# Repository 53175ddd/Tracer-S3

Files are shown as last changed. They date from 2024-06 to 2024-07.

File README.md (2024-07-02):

# 基板概要

JLCPCB の PCBA に対応した，私 [MOS](https://x.com/53175ddd) 作成のオリジナルライントレーサです  
表面実装部品（ESP32-S3 モジュール・SMD 抵抗・コンデンサ・レギュレータ・ダイオード）のみ PCBA で実装してくれるようにしています  
それ以外の部品については下記部品表を参考に，必要に応じて部品を変更するなどしてご利用ください

# イメージ

<div align="center">
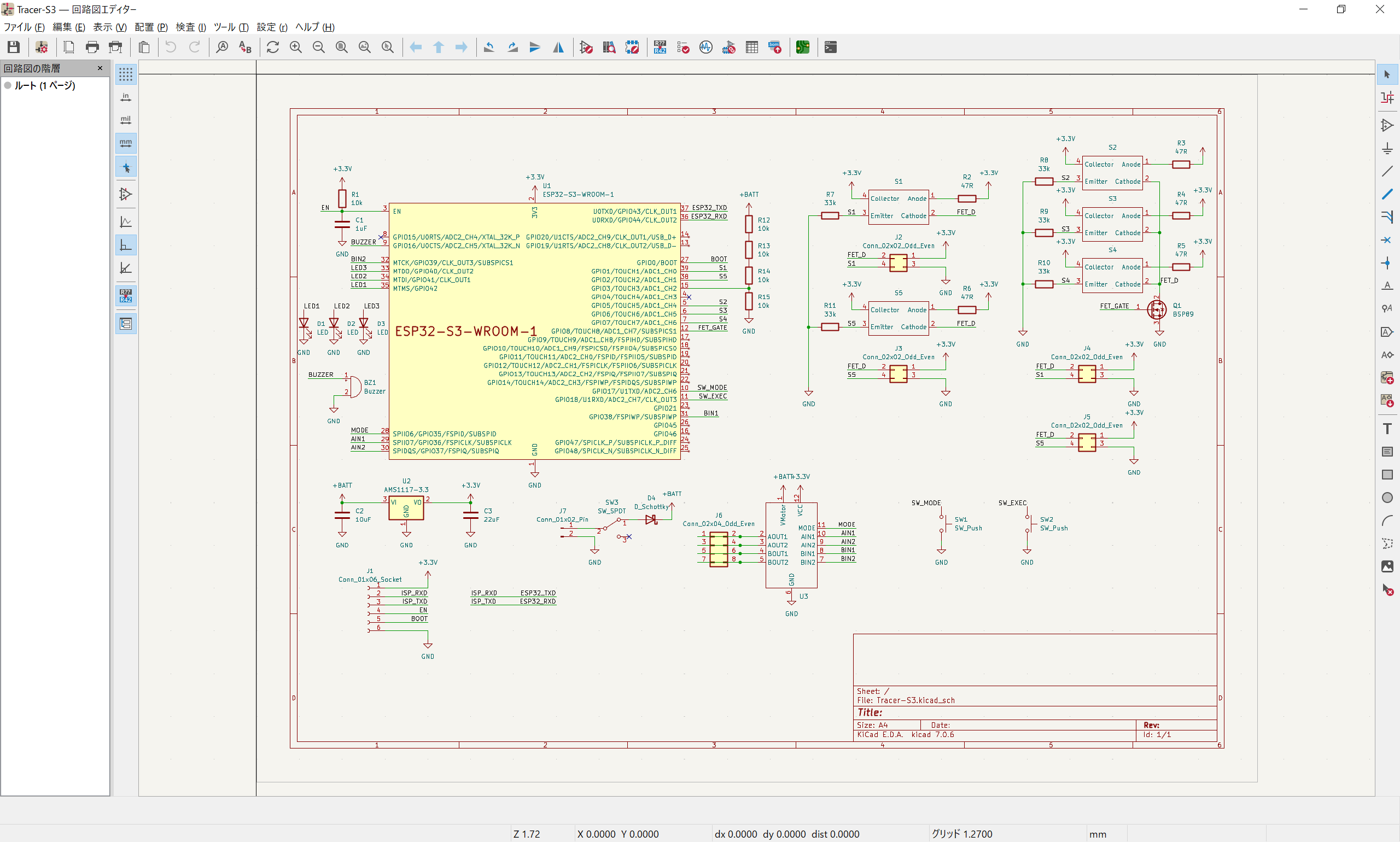
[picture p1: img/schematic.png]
  
</div>

# 部品表

| 部品番号 | 定数 | 秋月 |
|----|----|----|
| R2 ~ R6 | 47Ω 1/4W | <https://akizukidenshi.com/catalog/g/g125470/> |
| R7 ~ R11 | 3.3kΩ ~ 4.7kΩ 1/4W | 省略 |
| SW1, SW2 | タクトスイッチ | <https://akizukidenshi.com/catalog/g/g103648/> |
| SW3 | DPDT スイッチ | <https://akizukidenshi.com/catalog/g/g102627/> |
| Q1 | MOSFET | <https://akizukidenshi.com/catalog/g/g107597/> |
| U3 | モータドライバ DRV8835 | <https://akizukidenshi.com/catalog/g/g109848/> |
| BZ1 | ブザー | <https://akizukidenshi.com/catalog/g/g104118/> |
| J1 | 1x6 ピンソケット | <https://akizukidenshi.com/catalog/g/g103784/> |
| J2, J3 | 2x2 ピンヘッダ | <https://akizukidenshi.com/catalog/g/g116792/> |
| J6 | 2x4 ピンヘッダ | <https://akizukidenshi.com/catalog/g/g116793/> |
| J7 | バッテリコネクタ | 使用するバッテリに合うものを使用してください |
| D1 ~ D3 | 5V 抵抗内蔵 LED | <https://akizukidenshi.com/catalog/g/g106247/> |
| S1 ~ S5 | フォトセンサ LBR-127HLD | <https://akizukidenshi.com/catalog/g/g104500/> |

# その他部品

- タミヤ ギアボックス
- Li-Po バッテリ（2S）など
- Stamp ISP

がそれぞれ必要になります

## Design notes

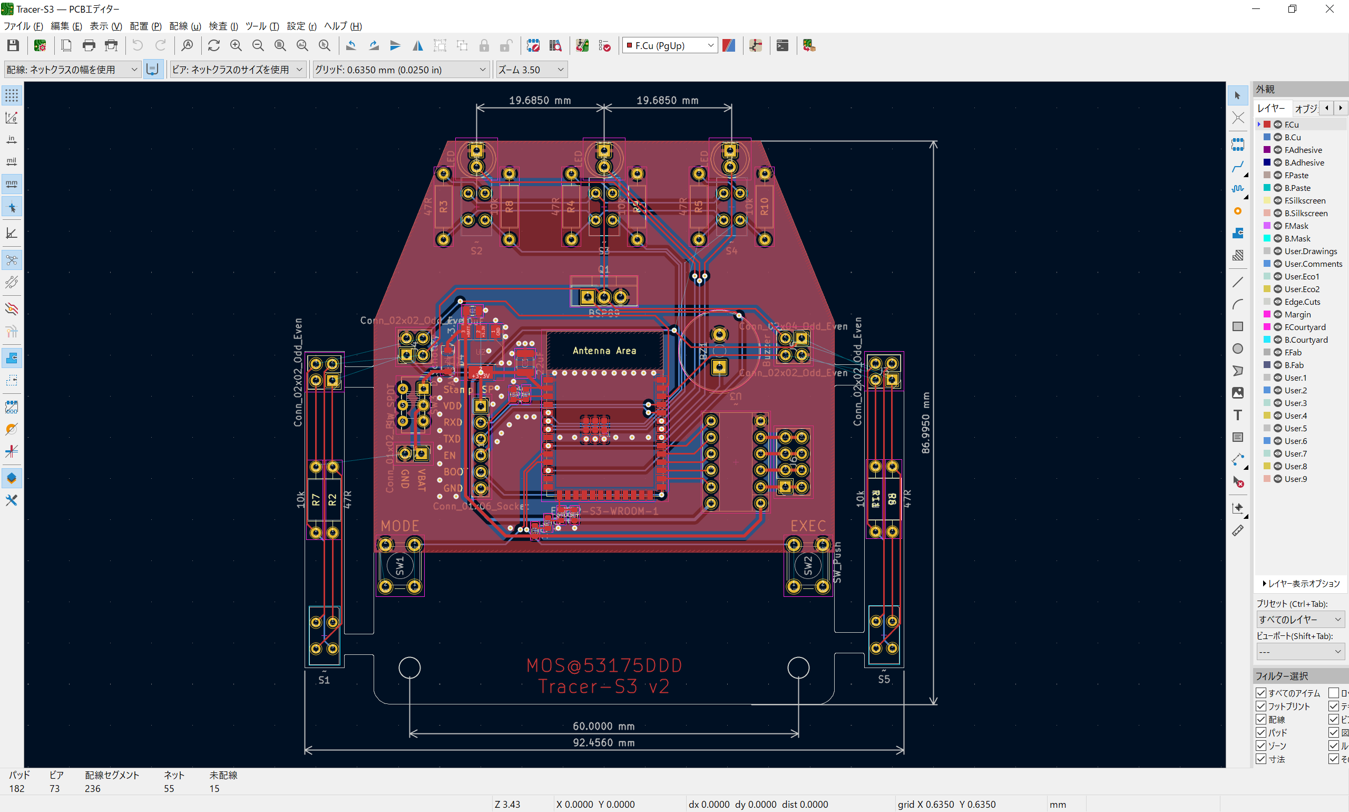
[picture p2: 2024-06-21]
img/pcb_editor.png

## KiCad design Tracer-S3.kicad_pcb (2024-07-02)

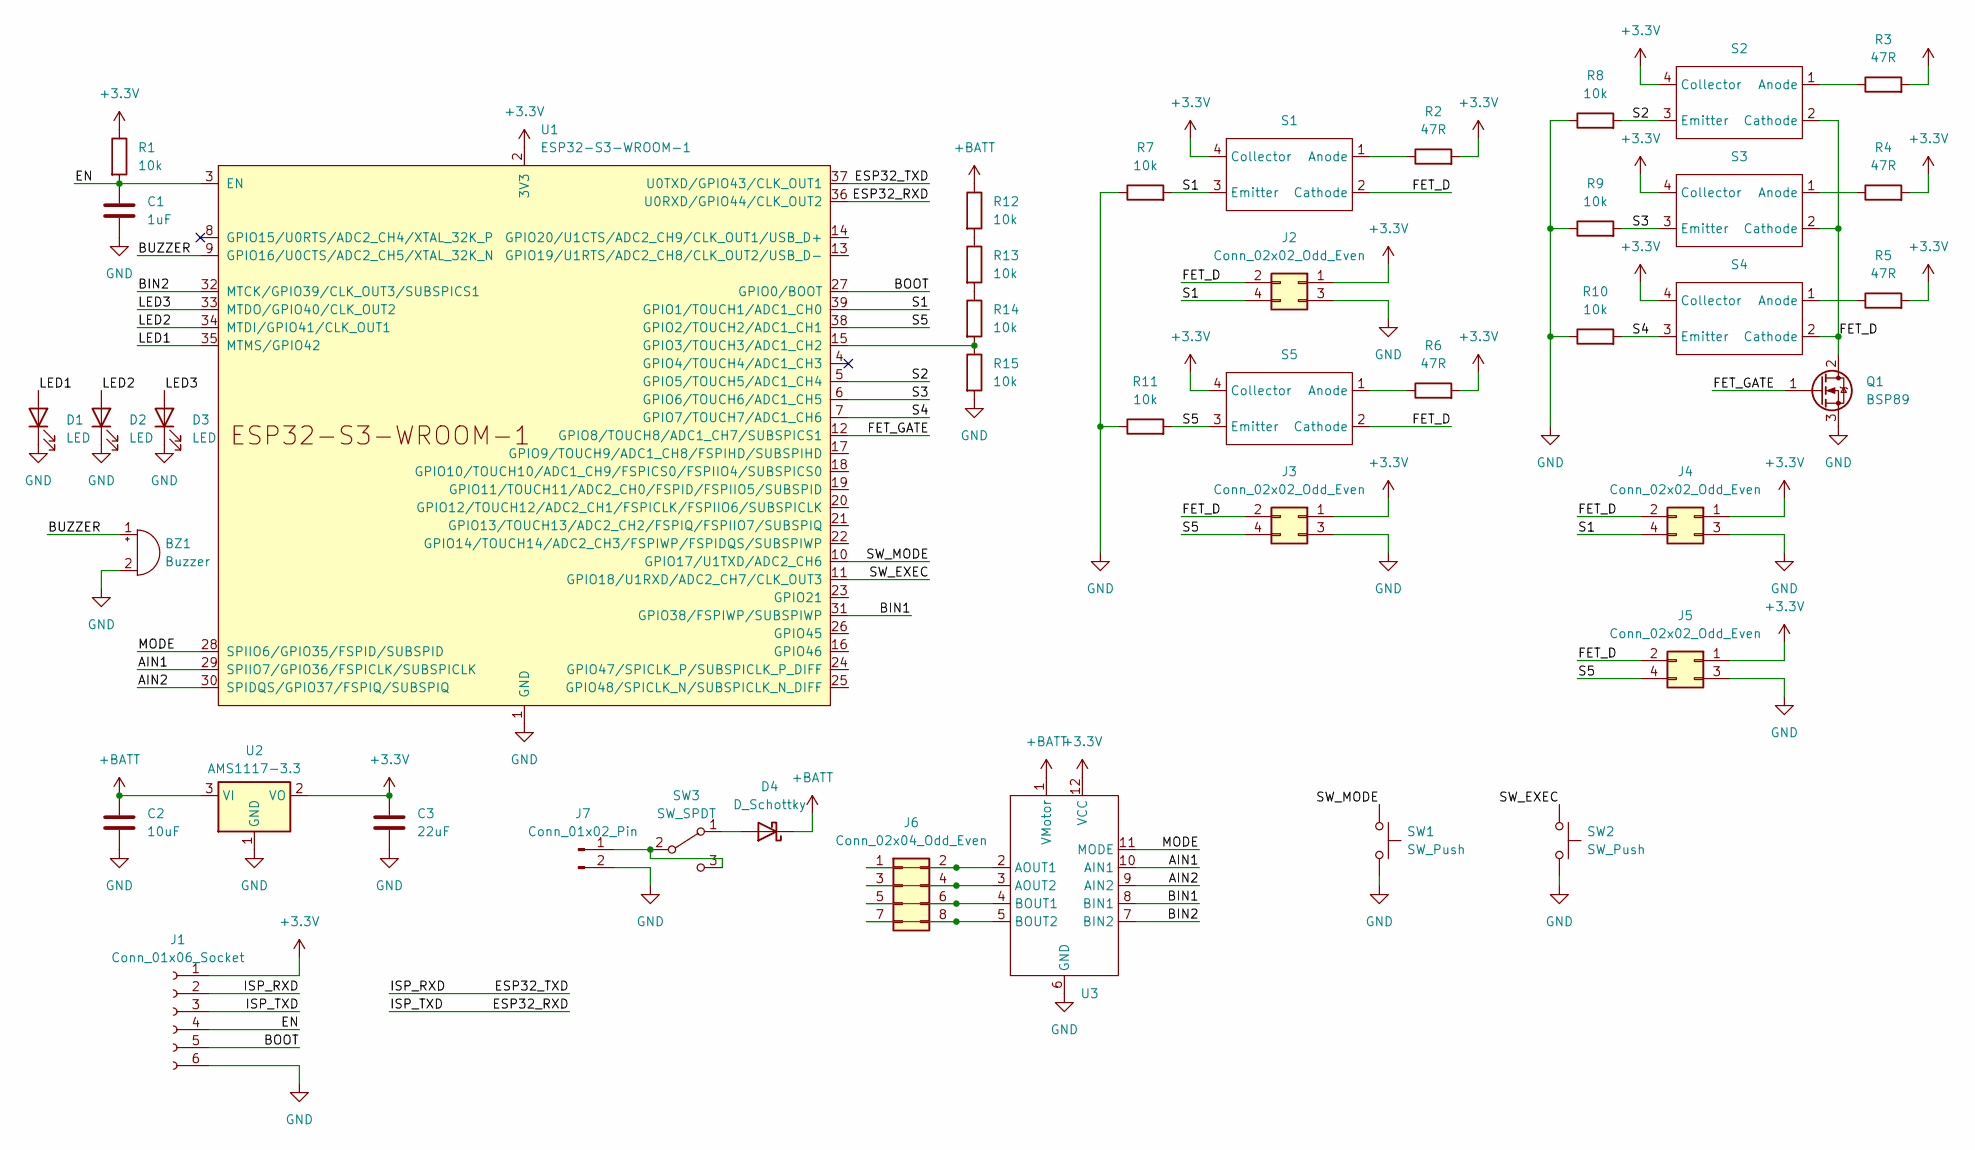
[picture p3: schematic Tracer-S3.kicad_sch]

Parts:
BZ1: Buzzer; Buzzer_TDK_PS1240P02BT_D12.2mm_H6.5mm
C1: 1uF; C_0603_1608Metric; LCSC C908011
C2: 10uF; C_0805_2012Metric; LCSC C162317
C3: 22uF; C_1210_3225Metric; LCSC C703078
D1, D2, D3: LED; LED_D5.0mm
D4: D_Schottky; D_SOD-123; LCSC C963381
J1: Conn_01x06_Socket; PinSocket_1x06_P2.54mm_Vertical
J2, J3, J4, J5: Conn_02x02_Odd_Even; PinSocket_2x02_P2.54mm_Vertical
J6: Conn_02x04_Odd_Even; PinSocket_2x04_P2.54mm_Vertical
J7: Conn_01x02_Pin; PinHeader_1x02_P2.54mm_Vertical
Q1: BSP89; TO-220-3_Vertical
R1, R12, R13, R14, R15: 10k; R_0603_1608Metric; LCSC C269701
R2, R3, R4, R5, R6: 47R; R_Axial_DIN0207_L6.3mm_D2.5mm_P10.16mm_Horizontal
R7, R8, R9, R10, R11: 10k; R_Axial_DIN0207_L6.3mm_D2.5mm_P10.16mm_Horizontal
S1, S2, S3, S4, S5: LBR-127HLD
SW1, SW2: SW_Push; SW_PUSH_6mm
SW3: SW_SPDT; SW_E-Switch_EG1271_SPDT
U1: ESP32-S3-WROOM-1
U2: AMS1117-3.3; SOT-223-3_TabPin2; LCSC C7432020
U3: AE-DRV8835

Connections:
+3.3V: C3.1, J1.1, J2.1, J3.1, J4.1, J5.1, R1.1, R2.2, R3.2, R4.2, R5.2, R6.2, S1.4 (Collector), S2.4 (Collector), S3.4 (Collector), S4.4 (Collector), S5.4 (Collector), U1.2 (3V3), U2.2 (VO), U3.12 (VCC)
+BATT: C2.1, D4.1 (K), R12.1, U2.3 (VI), U3.1 (VMotor)
/AIN1: U1.29 (SPIIO7/GPIO36/FSPICLK/SUBSPICLK), U3.10 (AIN1)
/AIN2: U1.30 (SPIDQS/GPIO37/FSPIQ/SUBSPIQ), U3.9 (AIN2)
/BIN1: U1.31 (GPIO38/FSPIWP/SUBSPIWP), U3.8 (BIN1)
/BIN2: U1.32 (MTCK/GPIO39/CLK_OUT3/SUBSPICS1), U3.7 (BIN2)
/BOOT: J1.5, U1.27 (GPIO0/BOOT)
/BUZZER: BZ1.1 (-), U1.9 (GPIO16/U0CTS/ADC2_CH5/XTAL_32K_N)
/EN: C1.1, J1.4, R1.2, U1.3 (EN)
/ESP32_RXD: J1.3, U1.36 (U0RXD/GPIO44/CLK_OUT2)
/ESP32_TXD: J1.2, U1.37 (U0TXD/GPIO43/CLK_OUT1)
/FET_D: J2.2, J3.2, J4.2, J5.2, Q1.2 (D), S1.2 (Cathode), S2.2 (Cathode), S3.2 (Cathode), S4.2 (Cathode), S5.2 (Cathode)
/FET_GATE: Q1.1 (G), U1.12 (GPIO8/TOUCH8/ADC1_CH7/SUBSPICS1)
/LED1: D1.2 (A), U1.35 (MTMS/GPIO42)
/LED2: D2.2 (A), U1.34 (MTDI/GPIO41/CLK_OUT1)
/LED3: D3.2 (A), U1.33 (MTDO/GPIO40/CLK_OUT2)
/MODE: U1.28 (SPIIO6/GPIO35/FSPID/SUBSPID), U3.11 (MODE)
/S1: J2.4, J4.4, R7.2, S1.3 (Emitter), U1.39 (GPIO1/TOUCH1/ADC1_CH0)
/S2: R8.2, S2.3 (Emitter), U1.5 (GPIO5/TOUCH5/ADC1_CH4)
/S3: R9.2, S3.3 (Emitter), U1.6 (GPIO6/TOUCH6/ADC1_CH5)
/S4: R10.2, S4.3 (Emitter), U1.7 (GPIO7/TOUCH7/ADC1_CH6)
/S5: J3.4, J5.4, R11.2, S5.3 (Emitter), U1.38 (GPIO2/TOUCH2/ADC1_CH1)
/SW_EXEC: SW2.1, U1.11 (GPIO18/U1RXD/ADC2_CH7/CLK_OUT3)
/SW_MODE: SW1.1, U1.10 (GPIO17/U1TXD/ADC2_CH6)
GND: BZ1.2 (+), C1.2, C2.2, C3.2, D1.1 (K), D2.1 (K), D3.1 (K), J1.6, J2.3, J3.3, J4.3, J5.3, J7.2, Q1.3 (S), R7.1, R8.1, R9.1, R10.1, R11.1, R15.2, SW1.2, SW2.2, U1.1 (GND), U1.40 (GND), U1.41 (GND), U2.1 (GND), U3.6 (GND)
unnamed: D4.2 (A), SW3.1 (A)
unnamed: J6.1, J6.2, U3.2 (AOUT1)
unnamed: J6.3, J6.4, U3.3 (AOUT2)
unnamed: J6.5, J6.6, U3.4 (BOUT1)
unnamed: J6.7, J6.8, U3.5 (BOUT2)
unnamed: J7.1, SW3.2 (B), SW3.3 (C)
unnamed: R12.2, R13.1
unnamed: R13.2, R14.1
unnamed: R2.1, S1.1 (Anode)
unnamed: R3.1, S2.1 (Anode)
unnamed: R4.1, S3.1 (Anode)
unnamed: R5.1, S4.1 (Anode)
unnamed: R6.1, S5.1 (Anode)
unnamed: R14.2, R15.1, U1.15 (GPIO3/TOUCH3/ADC1_CH2)

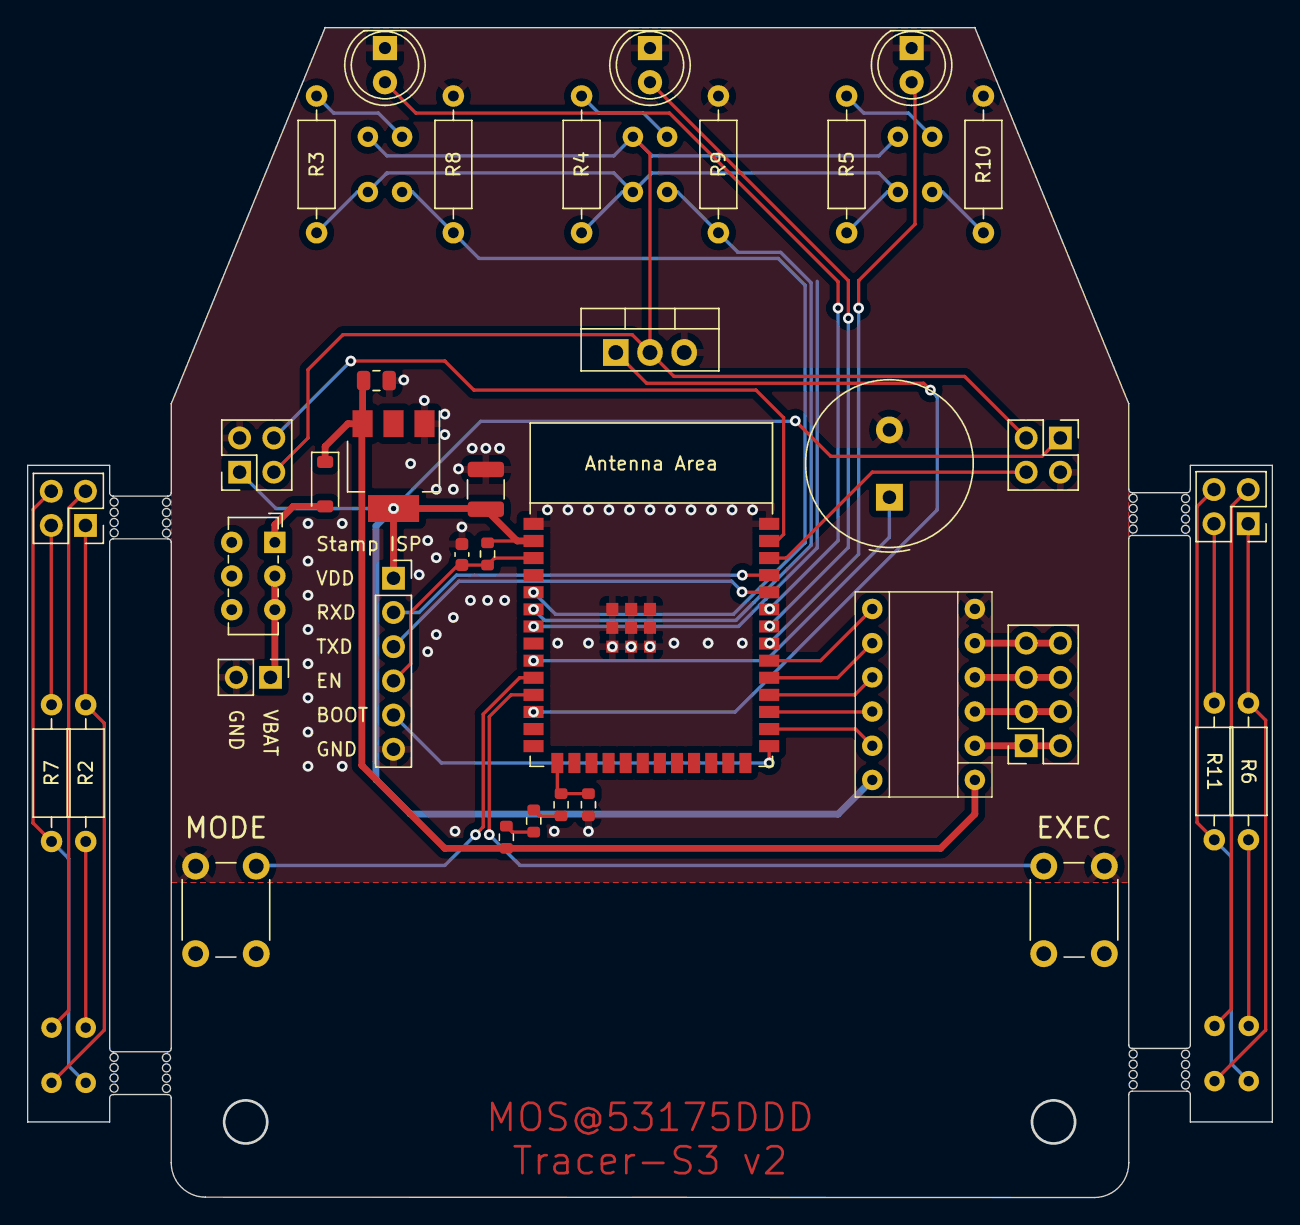
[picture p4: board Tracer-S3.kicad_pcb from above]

Board: 2 copper layers, 92.5 x 86.9 mm, 42 parts (0 on the bottom side), 39 nets.

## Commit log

2024-06-13 部品定数修正
    [Tracer-S3.kicad_sch]
2024-06-13 部品番号修正
    [Tracer-S3.kicad_pcb]
2024-06-14 部品変更
    フォトセンサの負荷抵抗を変更
    33k -> 10k
2024-06-18 回路定数変更
    [Tracer-S3.kicad_pcb, Tracer-S3.kicad_sch]
2024-06-21 センサ間隔調整・外形修正
    [Tracer-S3.kicad_pcb]
2024-07-02 電源スイッチ配線変更・ミシン穴追加
    [Tracer-S3.kicad_pcb, Tracer-S3.kicad_sch]
2024-07-02 負荷抵抗変更
